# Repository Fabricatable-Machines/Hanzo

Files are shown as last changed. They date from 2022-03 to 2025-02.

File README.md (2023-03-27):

# Hanzo - large format 3D printer and machining center

*by Jens Dyvik, August 2021 - ongoing*

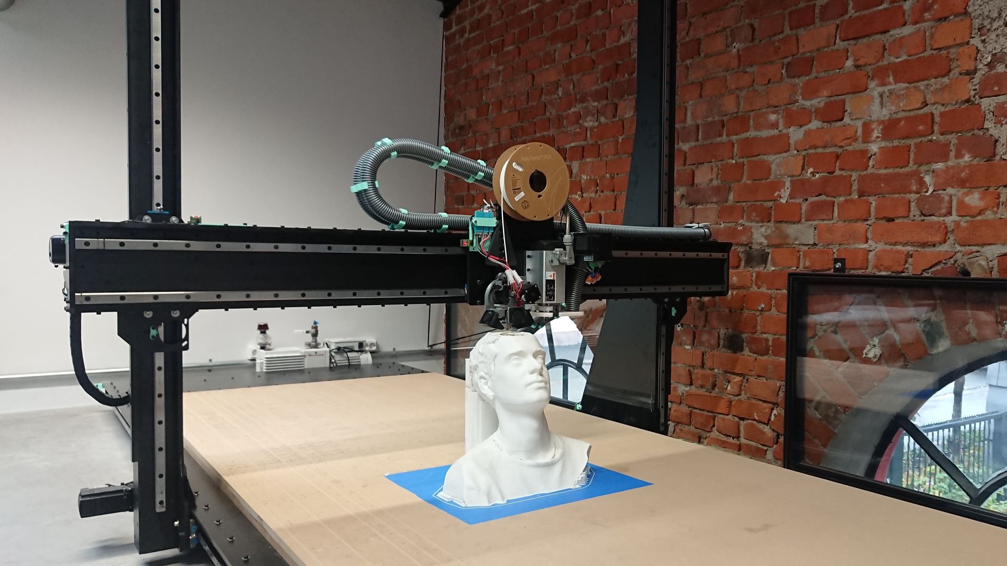
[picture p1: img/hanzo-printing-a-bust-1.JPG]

*Early test print of a 3D scan*

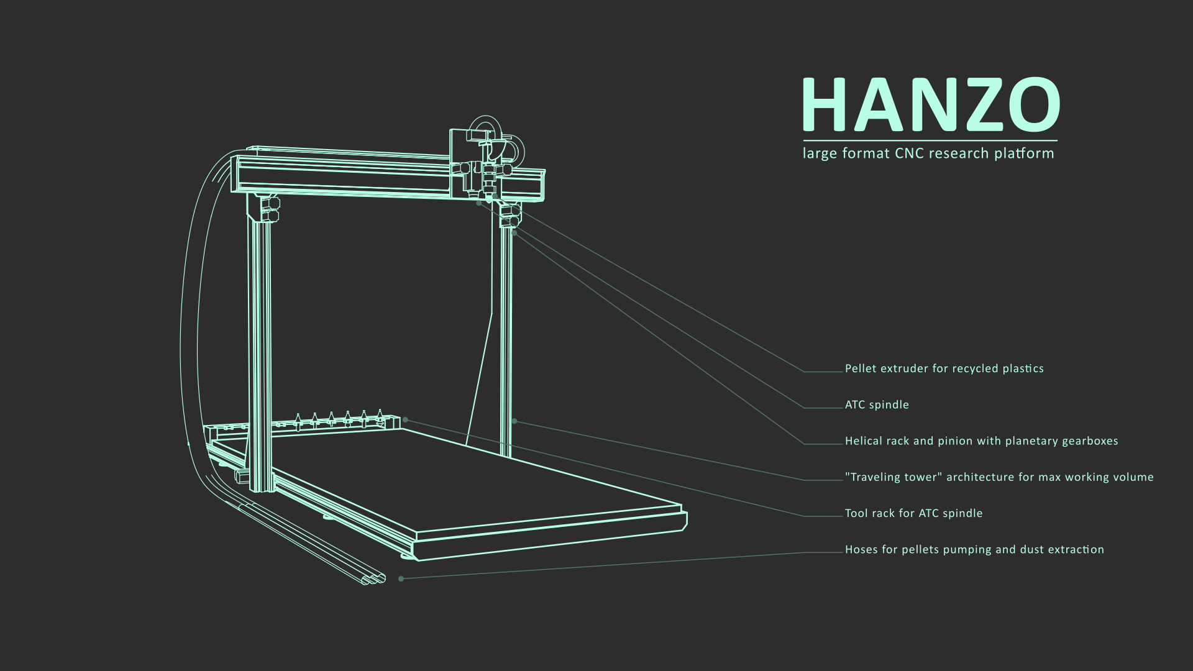
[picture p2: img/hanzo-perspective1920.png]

*The design plan*

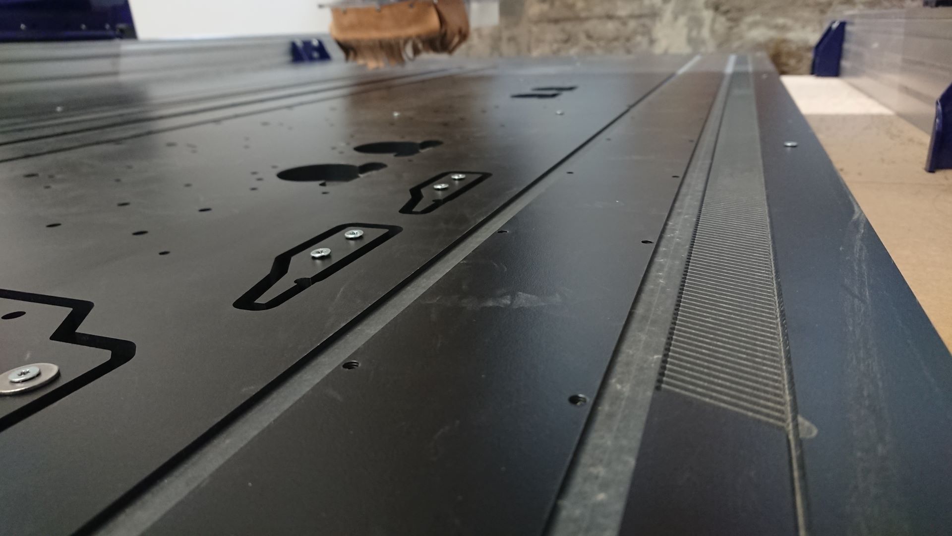
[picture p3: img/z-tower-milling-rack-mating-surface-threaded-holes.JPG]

*Milling parts for Hanzo on a ShopBot*

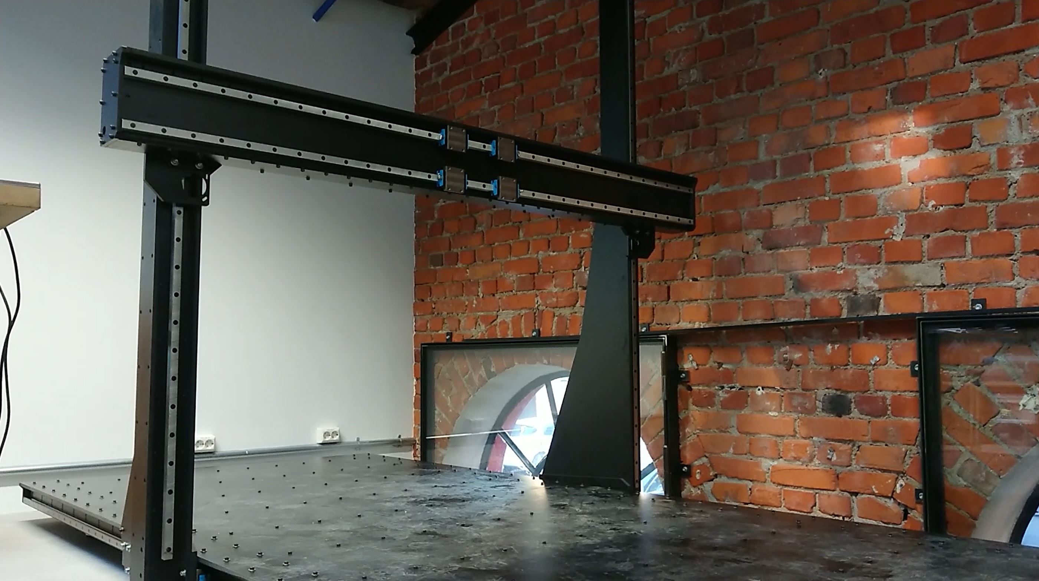
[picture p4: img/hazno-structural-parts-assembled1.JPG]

*Main structure assembled*

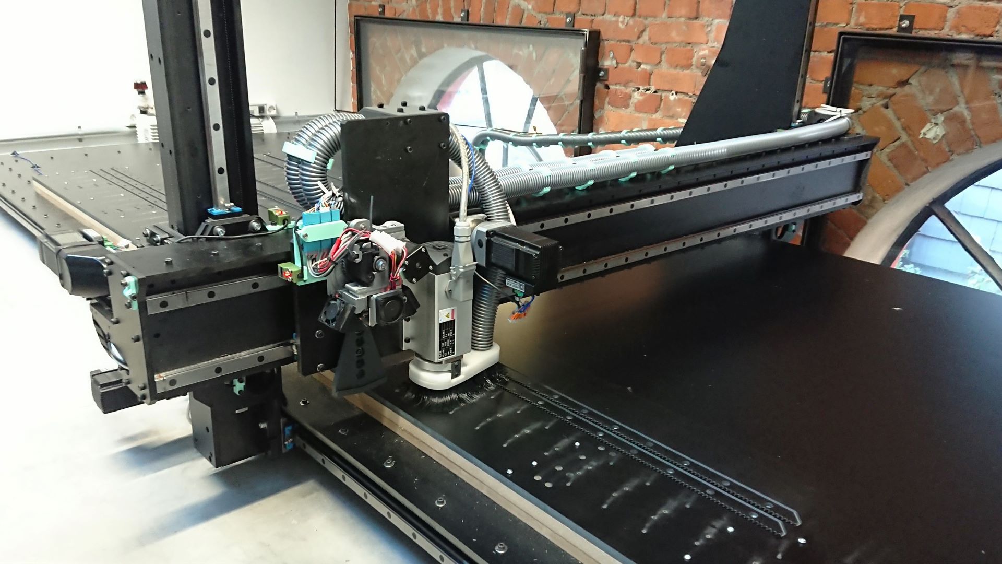
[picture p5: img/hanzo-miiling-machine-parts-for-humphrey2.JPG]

*Milling parts for [Humphrey2](https://github.com/Fabricatable-Machines/humphrey2) on Hanzo*


*Machine family tree. Hanzo succesully made the first [Humphrey2](https://github.com/Fabricatable-Machines/humphrey2) prototype, which again could replicate itself with acceptable precicion.*

### Project status

 - Currently under development. **Warning:** This experimental project is not recommended to reproduce, but the files can be used as a design reference.

### What

 - A cartesian machine with a 3m x 1,4m x 1,5m work area
 - Able to print rough and fast with the [Pellatis - pellet extruder](https://tobben.gitlab.io/pellatis/) that we are developing
 - With a toolchanger system
 - With 3D printed helical pinions and integrated machined helical racks
 - Tailor made to experiment with automation and machine making
 
### Why

 - I need a large machine with a lot of flexibility to do the research that I wont to do the coming years
 - If I have machine with a 3m long work area I can make machines with a 2,44m work area _(standard sheet size)_ for my local community in a single piece
 - I wan to make environmentally friendlier manufacturing methods more available
 - I want to making automation in digital fabrication more accessible

### How

 - I am looking to CNC mill almost all the the parts _(frame, rack, rails)_ from 12mm thick Trespa or other phenolic resin paper composite sheets

### Files

 - I am designing Hanzo in [Freecad]() *(free and open CAD software)*
 - I work in the open and publish and update the files in the [project folder](https://github.com/fellesverkstedet/fabricatable-machines/tree/master/hanzo-research-platform) of this repo
 - I also export .step files from freecad to the the [project folder](https://github.com/fellesverkstedet/fabricatable-machines/tree/master/hanzo-research-platform) that you can import into programs like Fusion360, Solidworks, Rhino etc.

### Support

 - If you appreciate this project you can support me on [Patreon](https://www.patreon.com/jensdyvik)
 - If you have design ideas and feedabck, pull requests and git issues are most welcome

### Log:

August 2021

 - The first parts of the machine has been fabricated. Making of video [here](https://youtu.be/XLuoENFNSG0)
 
October 2021

 - Too tight fit at ears on gantry gantry backplate (no tolerence, facepalm). Resorted to sanding. To do: add cleaance in CAD
 - Forgot to mill some pocket slots on gantry backsie (struggled with freecad step export)
 - Drilling ended up not entirely in center of slots
 - Whashers go over edge. to do check for collsions in CAD!
 - Array of threaded holes are missing in x axis plate.
 - One screw in upper bearing block is maybe too close
 - Hacked pocket and moved slots for gearbox
 - Large M5 whasers protrude over the edge. Uese button heads crews instead?
 - Forgot to offset motor protrusion slot to fit larger gearbox protrusion (fixe with 12mm offset and remill)
 - Nema23 gear is nema24 width (60mm) Tuning screw holder came too close to motor to allow pinion to completely disengage rack
 - Slot on gearbox does not run deep enough. Pinion protrudes more than planned. Tricky to solve becuse set screws need meat to sit in. Maybe skip using slot and rotate pinion 60 degrees?
 - double nut hack got too wide and the pinion set screws crshes into it. Needs s relief flot the diemter of the pinion set screw stickout +
 
 January-March 2022
 
 - Finished bed
 - Fabbed and assembled gantry and Z towers
 
 April 2022
 - Assembled structure
 
 May-June 2022
 - Electronics wiring and tidying up
 - Broke helical rack teeth on Z axis during testing
 
 August 2022
 - Retrofitted CNC friendly rack and pinion to Z axis
 
 September 2022
 - Milled out [Humphrey2](https://github.com/Fabricatable-Machines/humphrey2) on Hanzo

October 2022 
 - Test printing

### Attributions

 - Duet2 mounting plate by Mjolk https://www.thingiverse.com/thing:3525628/files

### License

Creative Commons Attribution-ShareAlike
http://creativecommons.org/licenses/by-sa/4.0/

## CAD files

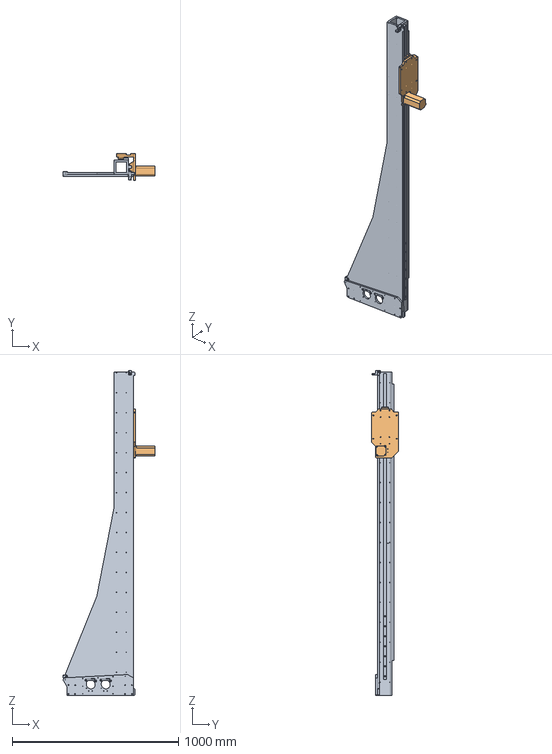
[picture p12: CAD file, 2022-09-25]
assembly-hanzo.FCStd
555.0 x 165.0 x 1953.0 mm
Z tower - right
Z carriage - right

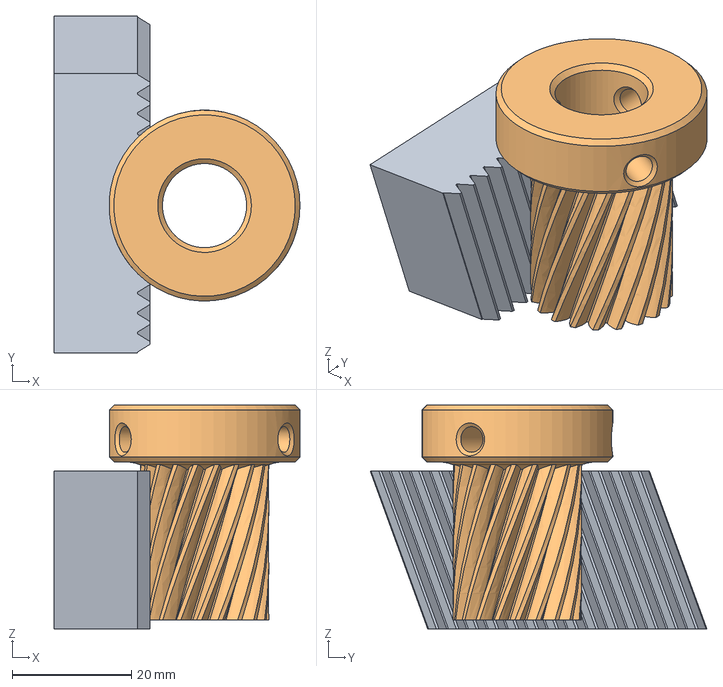
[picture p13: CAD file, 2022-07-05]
add-ons/19-tooth-pinion-for-5-1-gearbox.FCStd
41.2 x 56.5 x 37.5 mm
involuterack
Pinion - ready for print

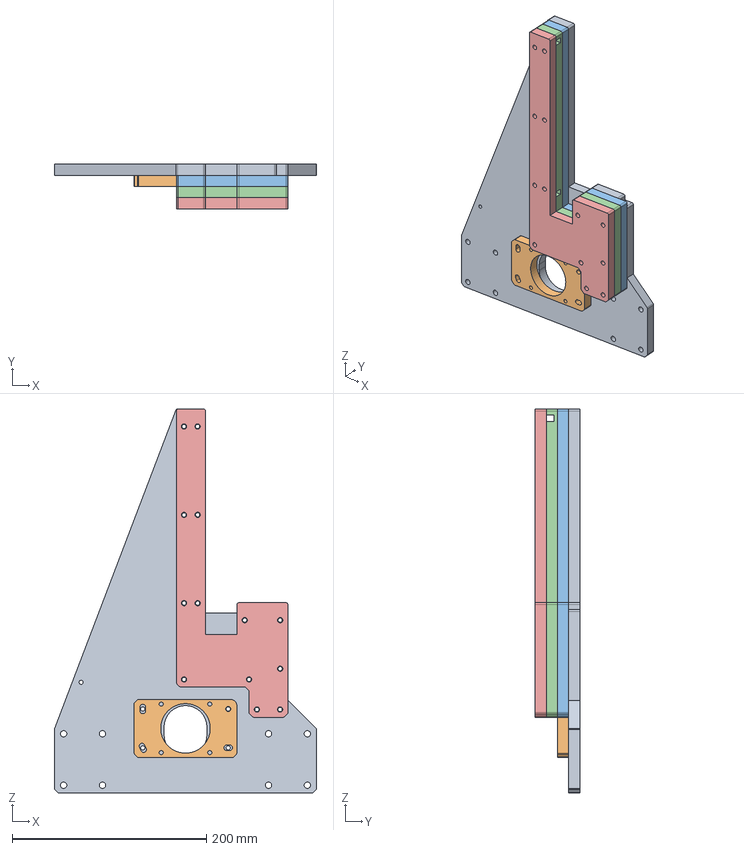
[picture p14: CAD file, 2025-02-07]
classic-gantry-conversion.FCStd
270.0 x 46.0 x 395.5 mm
Inner vertical plate
Motor plate001
First reinforcement wall
Second reinforcement wall - with holes
Third reinforcement wall

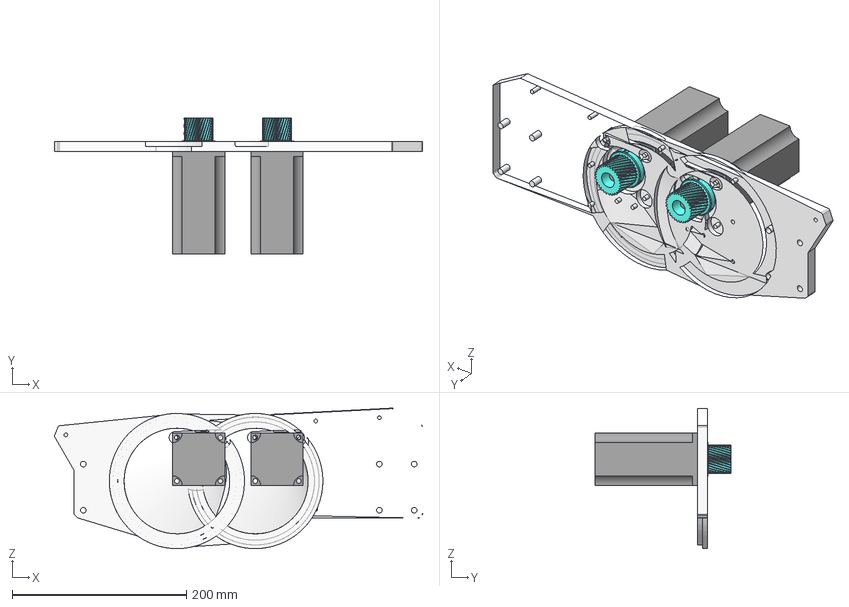
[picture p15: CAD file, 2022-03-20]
step-files/x-carriage-left.step
422.6 x 156.5 x 161.0 mm
Nema24 stepper motor002 x 2
30 tooth pinion x 2
Motor double lock nut x 2
X axis plate - with attachment thread holes cut

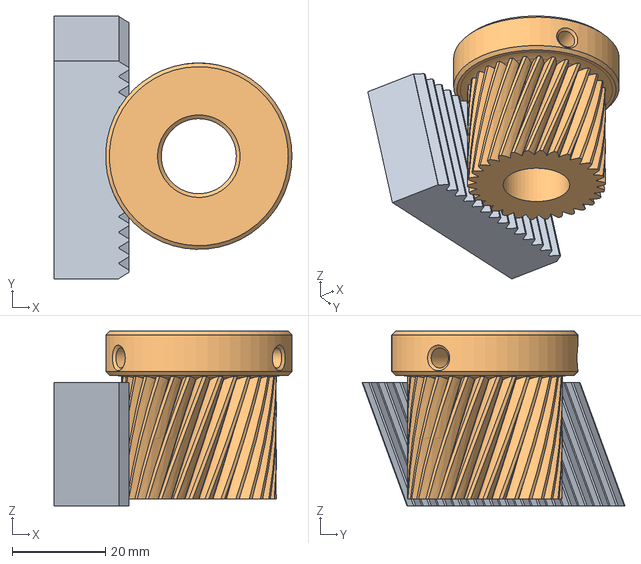
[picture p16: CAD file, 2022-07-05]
add-ons/30-tooth-pinion-for-10-1-gearbox.FCStd
51.1 x 56.5 x 37.5 mm
involuterack
Pinion - ready for print

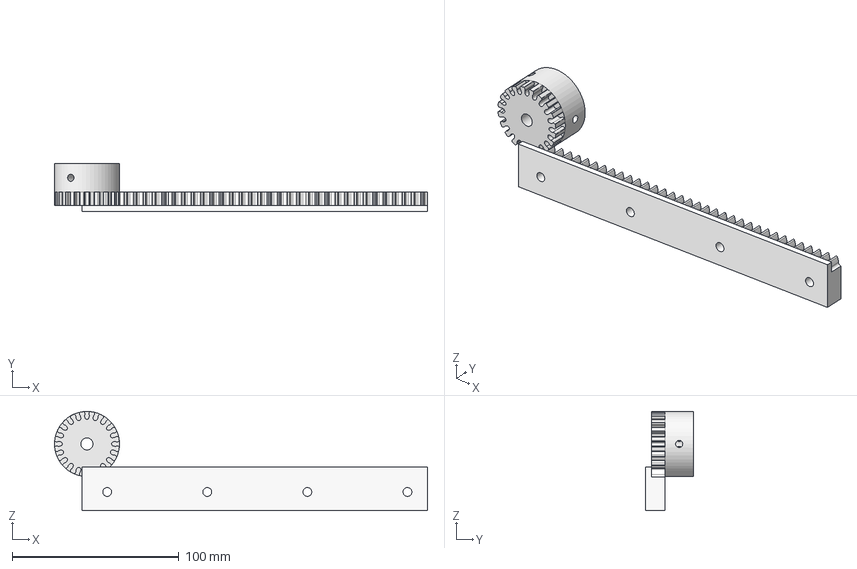
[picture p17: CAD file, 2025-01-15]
new-z-axis-for-classic-gantry-conversion.FCStd
223.6 x 28.6 x 59.4 mm
Rack with web and material thickness
Pinion

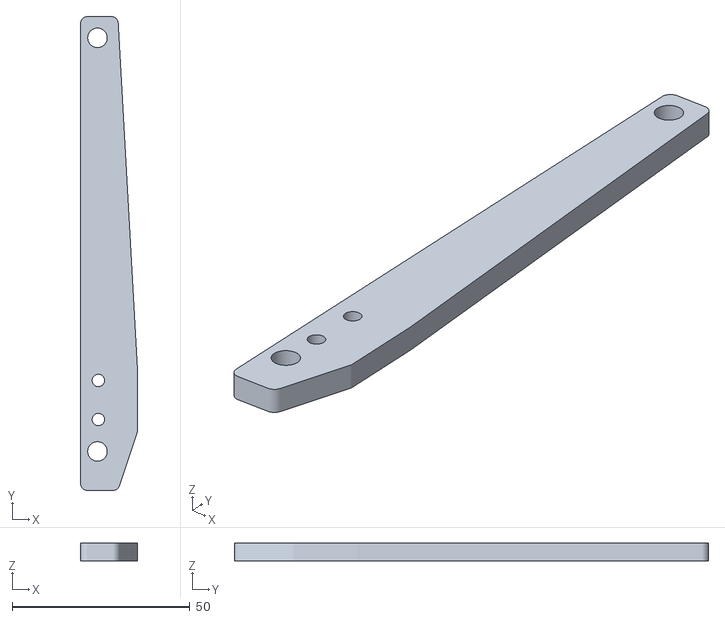
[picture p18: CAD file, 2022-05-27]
parts-to-3D-print/z-homing-sensor-holder.stl
16.0 x 133.5 x 5.00

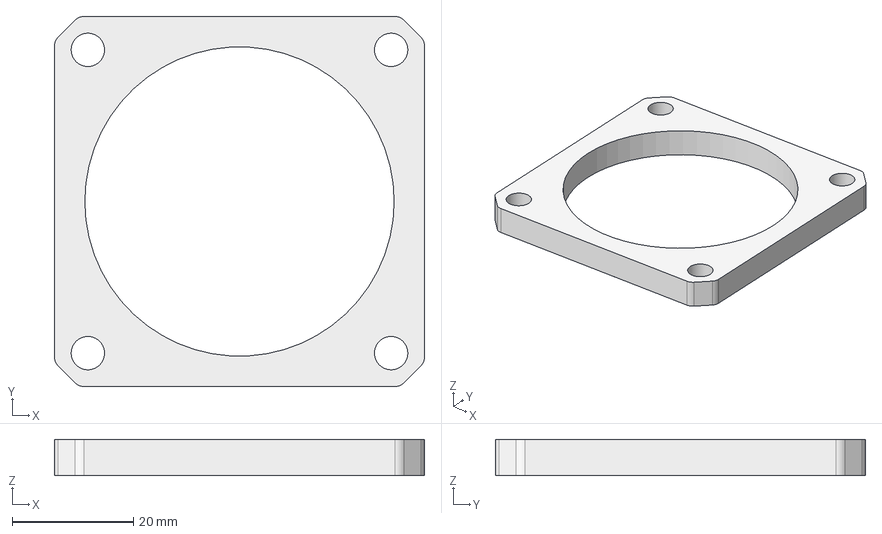
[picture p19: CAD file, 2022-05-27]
add-ons/nema23-gearbox-spacer.FCStd
61.0 x 61.0 x 6.00 mm

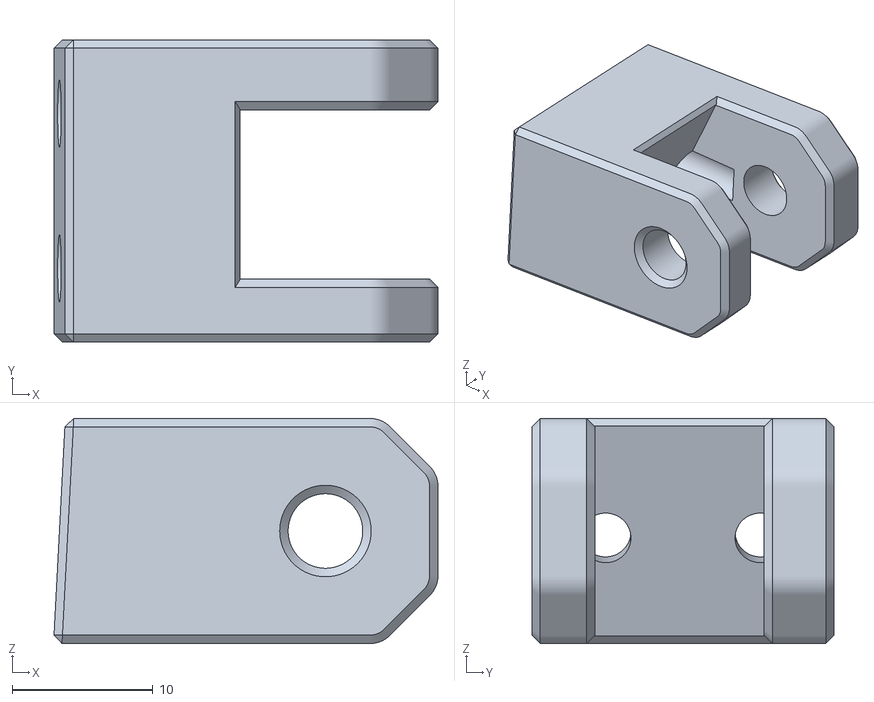
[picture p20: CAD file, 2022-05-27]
parts-to-3D-print/x-homing-sensor-holder.stl
27.3 x 21.5 x 16.0

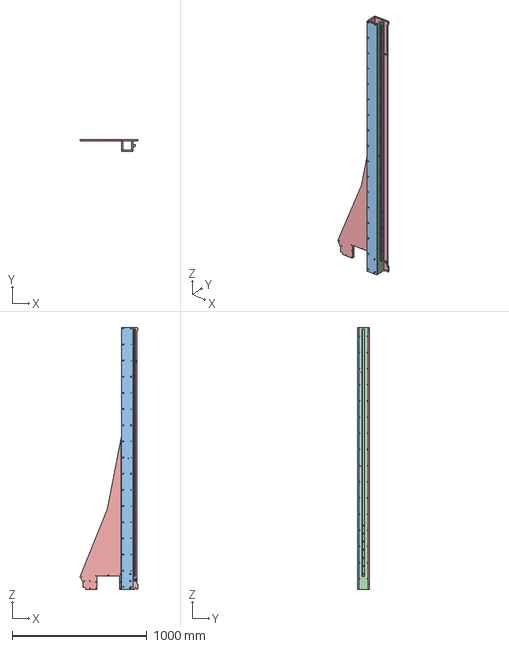
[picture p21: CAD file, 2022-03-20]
step-files/z-tower-left.step
431.1 x 87.5 x 1945.0 mm

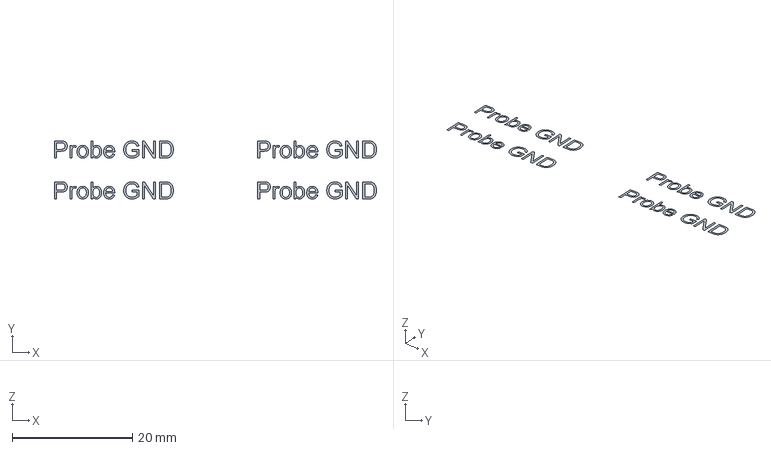
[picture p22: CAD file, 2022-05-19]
add-ons/label-maker-for-wiring.FCStd
53.5 x 9.65 x 0 mm

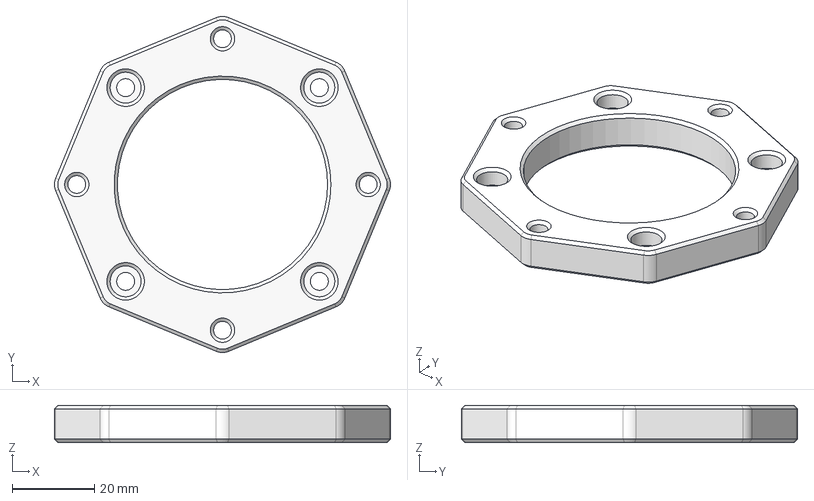
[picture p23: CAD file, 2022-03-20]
step-files/nema23-to-nema24-adapter.step
81.5 x 81.5 x 9.00 mm

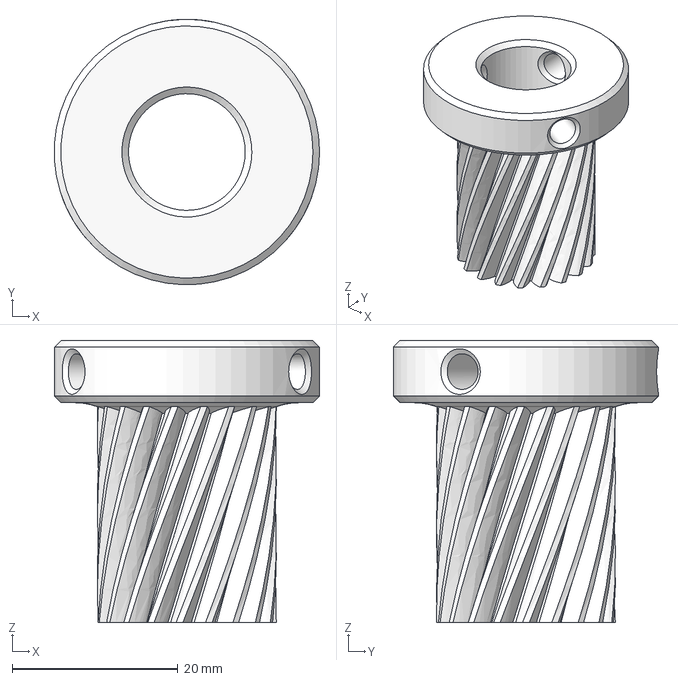
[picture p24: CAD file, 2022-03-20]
step-files/19-tooth-pinion-for-5-1-gearbox.step
32.0 x 32.0 x 34.0 mm

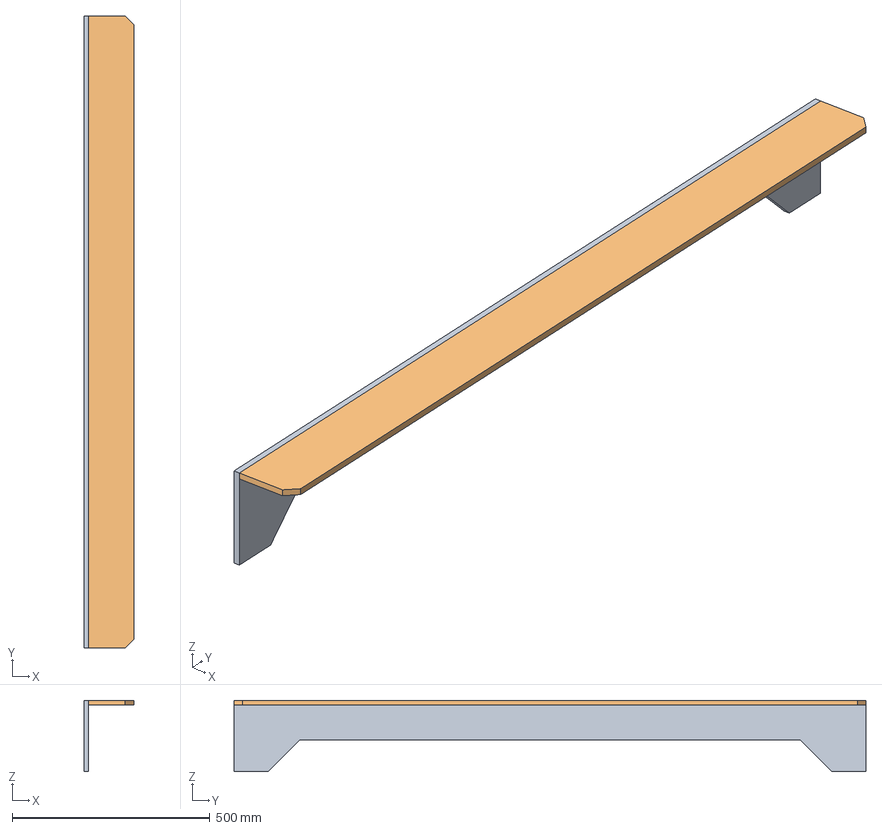
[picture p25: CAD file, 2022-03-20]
step-files/tower-connector.step
126.0 x 1598.0 x 180.0 mm
Connecting back plate
Connecting top plate

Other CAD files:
add-ons/festool-vaccum-cleaner-to-32mm-hose-adapter.FCStd
step-files/30-tooth-pinion-for-10-1-gearbox.step
add-ons/distancing-tool-rail-mounting-2mm.FCStd
parts-to-3D-print/festool-vaccum-cleaner-to-32mm-hose-adapter.stl
add-ons/distancing-tool-rail-mounting-2mm.stl
add-ons/double-nut-with-trapped-m5-nuts.FCStd
add-ons/e-chain-bracket.FCStd
add-ons/end-stop-front.FCStd
add-ons/gearbox-and-motor-90-deg-mount-for-electronics-testing.FCStd
add-ons/homing-screw-holder.FCStd
add-ons/hose-clamp-40mm-bottom-with-double-screws.FCStd
add-ons/m3-screw-protection-cap.FCStd
add-ons/motor-mount-holes-nema23.FCStd
add-ons/motor-mount-holes-nema23.step
add-ons/motor-mount-holes-nema24.FCStd
add-ons/motor-mount-holes-nema24.step
add-ons/motor-mount-slots-with-tuning.FCStd
add-ons/nema23-hole-lid.FCStd
add-ons/nema23-stepper-motor.FCStd
add-ons/nema23-to-nema24-adapter.FCStd
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

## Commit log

2022-03-20 Migrated hanzo project
    [19-tooth-pinion-for-5-1-gearbox.FCStd, 19-tooth-pinion-for-5-1-gearbox.step, 30-tooth-pinion-for-10-1-gearbox.FCStd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]
2022-03-21 reduced chamfer size in order to reduce warping during print
    [hose-clamps-40mm.stl]
2022-03-28 house keeping
    [19-tooth-pinion-for-5-1-gearbox.FCStd, 30-tooth-pinion-for-10-1-gearbox.FCStd, end-stop-front.FCStd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]
2022-05-15 label maker and 3D printed parts
    [homing-screw-holder.FCStd, homing-screw-holder.stl, hose-clamp-40mm-bottom-with-double-screws.FCStd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]
2022-05-19 tweaked label maker
    [label-maker-for-wiring.FCStd]
2022-05-27 homing sensor work and pinion tweaks
    [19-tooth-pinion-for-5-1-gearbox.FCStd, 30-tooth-pinion-for-10-1-gearbox.FCStd, homing-screw-holder.stl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]
2022-05-31 homing design and bed work
    [x-homing-screw-holder.stl]
2022-07-05 tweaked dimensions
    [19-tooth-pinion-for-5-1-gearbox.FCStd, 30-tooth-pinion-for-10-1-gearbox.FCStd]
2022-07-05 added image of first test print to readme
2022-09-12 new improved assembly with links
2022-09-25 new rack retrofit for z axis
    [assembly-hanzo.FCStd]
2022-10-25 added images of print test
2022-10-25 added an image of milling machine parts on hanzo
2025-01-15 Started design work
    for a classic gantry conversion
    [classic-gantry-conversion.FCStd, new-z-axis-for-classic-gantry-conversion.FCStd]
2025-02-07 design progress
    [classic-gantry-conversion.FCStd]
2025-02-07 z axis design done
    [classic-gantry-conversion.FCStd]
